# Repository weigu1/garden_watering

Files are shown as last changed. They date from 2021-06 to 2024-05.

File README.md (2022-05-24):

# Watering the garden with valves per MQTT over WiFi using an ESP8266

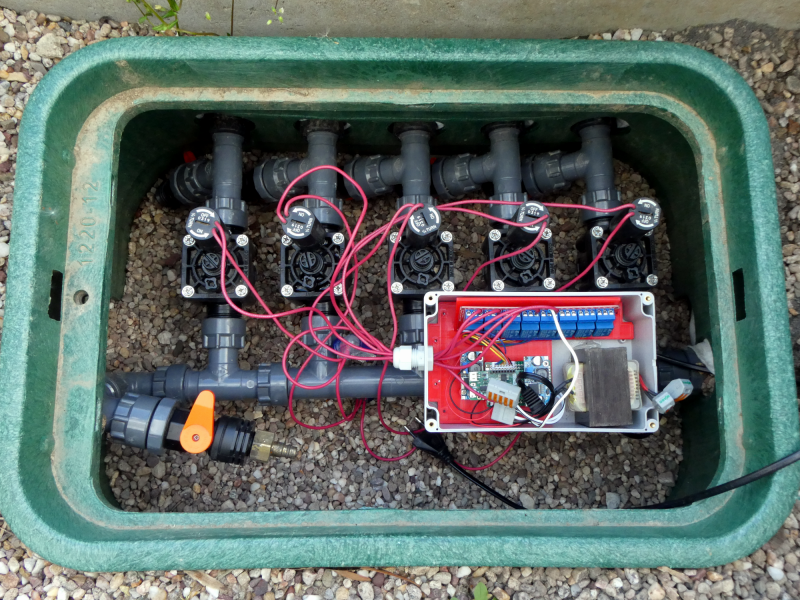
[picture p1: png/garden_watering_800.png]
garden_watering garden watering


## All infos on: <http://www.weigu.lu/microcontroller/garden_watering/index.html>

## Some infos

The vegetable garden must be regularly supplied with water. To save water, I use drip hoses, and to simplify my life, I have automated the control of the irrigation.

It began with a command of a box with 5 magnetic valves from Hunter. The box contained 5 valves Hunter PGV 101 MMB (3/4", 25&#8239;mm). The valves need 24&#8239;VAC, so we need a transformer. As the valves are never open at the same time a current of 1&#8239;A should suffice. There are cheap relay shields out there with Optocoupler, perfect for this project. An ESP8266 ([Lolin/Wemos D1 mini pro V2 ](https://www.wemos.cc/en/latest/d1/d1_mini_pro.html)) connects us with the network over WiFi and MQTT and is used to send commands and get data. The ESP8266 board is also powered by the transformer. This is done with a LM2596 DC/DC buck converter breakout board.

As the whole thing is contained in a  IP65 waterproof enclosure, I wanted to monitor temperature and humidity in the box and added a BMP280 sensor. A piece of PLA from my 3D printer created with FreeCAD (files on git) helped to connect everything together.

### BOM

- 5 valves Hunter PGV 101 MMB (3/4", 25&#8239;mm, 24&#8239;VAC)
- Trafo 24&#8239;VAC
- 8 Channel DC 5&#8239;V AC 230&#8239;V Relay Shield with Optocoupler
- LM2596 DC/DC Buck Converter
- Lolin/Wemos D1 mini pro V2
- BMP280 breakout board
- BOPLA ET-237 Euromas II, 200x120x90&#8239;mm³, IP65

### Software

The software communicates per `MQTT` over `WiFi`. It uses my ESPToolbox library for WiFi and logging functions and to get the time. To avoid version problems the lib is included in the sketch folder. Programming is done over OTA.

We get two topics:

```C
    String MQTT_TOPIC_OUT = "weigu/garden/watering/data";
    String MQTT_TOPIC_IN = "weigu/garden/watering/command";
```

Commands are in JSON and have the following JSON format (I eliminated the square brackets in the new version 1.1 because openHAB had problems with those when transforming):

```json
    {"Relay_(0-4)":4,"Time_min":20}
    {"Auto_(0-1)":1} 
    {"Event_(nr_relay_start_duration)":"3 3 2021 5"}   
```

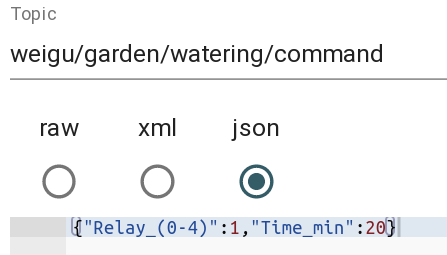
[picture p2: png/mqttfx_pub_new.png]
mqtt publish


+ With the first command you can start or stop manually the watering of a relay. Watering stops automatically after x minutes. To stop manually the time is set to zero: `{"Relay_(0-4)":4,"Time_min":0}`

+ The second command (version 1.1) switches automatic watering on (1) or off (0).

+ With the third command (version 1.1) we can also change via MQTT the watering events in the events array. Supported are up to 10 (0-9) events. Default are 5 events but you can add events in the `config.h` file. In the automated watering array we define the start times of a relay and duration of watering events. If we want e.g. that relay 3 opens at 15h15 for 15 minutes we add the line: `{3,1515,15}` to the array. With the command: `{"Event_(nr_relay_start_duration)":"3 3 2021 5"}` we can change this. The first number is the event number (0-9).   

The following is seen on the data channel:

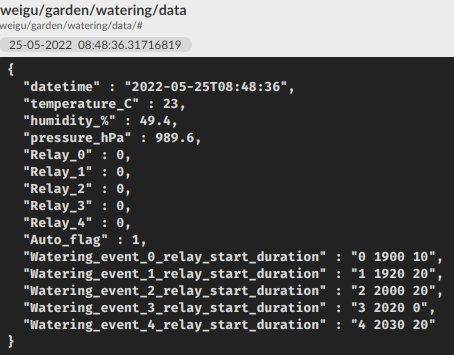
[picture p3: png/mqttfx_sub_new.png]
mqtt subscribe


In the new version  (1.1) all relevant data you must or can change are in a config (`config.h`) file, also contained in the main folder. You can also place this file in the sketchbook/library folder named `Secrets` and rename it to your needs (e.g. `secrets.h`).

In the main file (.ino) you can activate or deactivate features by commenting or uncommenting some lines. Here you must activate `USE_SECRETS`:

In the `config.h` file, you must change the WiFi parameter and the MQTT server address. In the automated watering array we define the start times and duration of watering events.

Other things we perhaps want to change are the publishing interval `PUBLISH_TIME` or the MQTT topics.

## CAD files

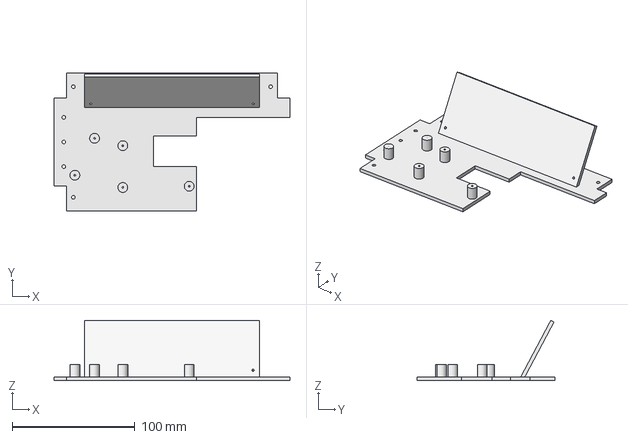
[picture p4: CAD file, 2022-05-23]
FreeCAD/pcb_holder.FCStd
192.0 x 112.0 x 49.1 mm

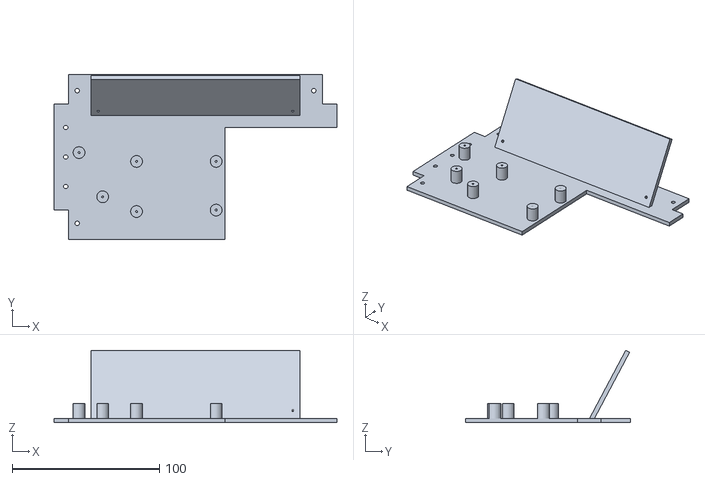
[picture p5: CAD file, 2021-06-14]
FreeCAD/pcb_holder-Fusion001.stl
192.0 x 112.0 x 49.1

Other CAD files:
FreeCAD/pcb_holder.stl

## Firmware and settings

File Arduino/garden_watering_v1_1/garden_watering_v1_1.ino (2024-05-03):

/*
  garden_watering.ino

  V1.1 2022-05-23
  changes from v1.0: added config file, mqtt secure bug, added scheduled
                     erigation.
                      
  for infos over time:
  https://www.weigu.lu/microcontroller/tips_tricks/esp_NTP_tips_tricks/index.html                   

  ---------------------------------------------------------------------------
  Copyright (C) 2022 Guy WEILER www.weigu.lu
  
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
  This program is distributed in the hope that it will be useful,
  but WITHOUT ANY WARRANTY; without even the implied warranty of
  MERCHANTABILITY or FITNESS FOR A PARTICULAR PURPOSE.  See the
  GNU General Public License for more details.
  You should have received a copy of the GNU General Public License
  along with this program.  If not, see <https://www.gnu.org/licenses/>.
  ---------------------------------------------------------------------------
 
  ESP8266: LOLIN/WEMOS D1 mini pro
  ESP32:   MH ET LIVE ESP32-MINI-KIT 
  
  MHET    | MHET    - LOLIN        |---| LOLIN      - MHET    | MHET
  
  GND     | RST     - RST          |---| TxD        - RxD(3)  | GND
   NC     | SVP(36) -  A0          |---| RxD        - TxD(1)  | 27 
  SVN(39) | 26      -  D0(16)      |---|  D1(5,SCL) -  22     | 25
   35     | 18      -  D5(14,SCK)  |---|  D2(4,SDA) -  21     | 32
   33     | 19      -  D6(12,MISO) |---|  D3(0)     -  17     | TDI(12)
   34     | 23      -  D7(13,MOSI) |---|  D4(2,LED) -  16     | 4
  TMS(14) | 5       -  D8(15,SS)   |---| GND        - GND     | 0   
   NC     | 3V3     - 3V3          |---|  5V        -  5V     | 2
  SD2(9)  | TCK(13)                |---|              TD0(15) | SD1(8)
  CMD(11) | SD3(10)                |---|              SD0(7)  | CLK(6)
*/

/*!!!!!!!!!! make your changes in config.h (or secrets.h) !!!!!!!!!*/

/*!!!!!!!!!! to debug you can use the onboard LED, a second serial port on D4
             or best: UDP! Look in setup()                !!!!!!!!!*/
             
/*?????? Comment or uncomment the following lines suiting your needs ??????*/

/* The file "secrets.h" (here secrets_garden.h) has to be placed in the sketchbook libraries folder
   in a folder named "Secrets" and must contain the same things than the file config.h*/
#define USE_SECRETS
#define OTA               // if Over The Air update needed (security risk!)
//#define MQTTPASSWORD    // if you want an MQTT connection with password (recommended!!)
#define STATIC            // if static IP needed (no DHCP)
#define BME280_I2C       

/****** Arduino libraries needed ******/
#ifdef USE_SECRETS
  #include <secrets_garden_watering.h>
#else  
  #include "config.h"      // most of the things you need to change are here
#endif // USE_SECRETS  
#include "ESPToolbox.h"  // ESP helper lib (more on weigu.lu)
#include <PubSubClient.h>
#include <ArduinoJson.h>
#ifdef BME280_I2C
  #include <Wire.h>
  #include <BME280I2C.h>
#endif

/****** WiFi and network settings ******/
const char *WIFI_SSID = MY_WIFI_SSID;           // if no secrets file, use the config.h file
const char *WIFI_PASSWORD = MY_WIFI_PASSWORD;   // if no secrets file, use the config.h file
#ifdef OTA                                // Over The Air update settings
  const char *OTA_NAME = MY_OTA_NAME;
  const char *OTA_PASS_HASH = MY_OTA_PASS_HASH;  // use the config.h file
#endif // ifdef OTA      
#ifdef STATIC
  IPAddress NET_LOCAL_IP (NET_LOCAL_IP_BYTES);    // 3x optional for static IP
  IPAddress NET_GATEWAY (NET_GATEWAY_BYTES);      // look in config.h
  IPAddress NET_MASK (NET_MASK_BYTES);  
#endif // ifdef STATIC
IPAddress UDP_LOG_PC_IP(UDP_LOG_PC_IP_BYTES);     // UDP logging if enabled in setup() (config.h)

/****** MQTT settings ******/
const int MQTT_MAXIMUM_PACKET_SIZE = 2048; // in setup()
const short MQTT_PORT = MY_MQTT_PORT;
WiFiClient espClient;
#ifdef MQTTPASSWORD
  const char *MQTT_USER = MY_MQTT_USER;
  const char *MQTT_PASS = MY_MQTT_PASS;
#endif // MQTTPASSWORD

PubSubClient MQTT_Client(espClient);

/******* BME280 ******/
float temp(NAN), hum(NAN), pres(NAN);
#ifdef BME280_I2C
  BME280I2C bme;    // Default : forced mode, standby time = 1000 ms
                    // Oversampling = pressure ×1, temperature ×1, humidity ×1, filter off,
#endif

ESPToolbox Tb;

/********** SETUP ************************************************************/
void setup() {
  Tb.set_led_log(true);                 // use builtin LED for debugging
  //Tb.set_serial_log(true,1);        // 2 parameter = interface (1 = Serial1)  
  Tb.set_udp_log(true, UDP_LOG_PC_IP, UDP_LOG_PORT); // use "nc -kulw 0 7777"    
  Tb.init_ntp_time();  
  init_wifi();       
  init_relays(PIN_RELAYS,sizeof(PIN_RELAYS));
  #ifdef BME280_I2C
    init_bme280();     
  #endif
  delay(2000);                                  // give it some time   
  MQTT_Client.setBufferSize(MQTT_MAXIMUM_PACKET_SIZE);
  MQTT_Client.setServer(MQTT_SERVER,MQTT_PORT); //open connection MQTT server
  MQTT_Client.setCallback(MQTT_callback);
  //mqtt_connect();
  #ifdef OTA
    Tb.init_ota(OTA_NAME, OTA_PASS_HASH);
  #endif // ifdef OTA
  Tb.blink_led_x_times(3);
  Tb.log_ln("Setup done!");
}

/********** LOOP  ************************************************************/

void loop() {
  #ifdef OTA
    ArduinoOTA.handle();
  #endif // ifdef OTA
  Tb.get_time();
  handle_relays();
  handle_auto_watering();
  // Publish every PUBLISH_TIME  
  if (Tb.non_blocking_delay(PUBLISH_TIME)) {    
    MQTT_get_temp_and_publish();        
  }    
  if (WiFi.status() != WL_CONNECTED) {   // if WiFi disconnected, reconnect
    init_wifi();
  }    
  if (!MQTT_Client.connected()) {        // reconnect mqtt client, if needed  
    mqtt_connect();
  }
  MQTT_Client.loop();                    // make the MQTT live  
  delay(10); // needed for the watchdog!
}

/********** WiFi functions ***************************************************/

// init WiFi (overloaded function if STATIC)
void init_wifi() {
  #ifdef STATIC
    Tb.init_wifi_sta(WIFI_SSID, WIFI_PASSWORD, NET_HOSTNAME, NET_LOCAL_IP,
                  NET_GATEWAY, NET_MASK);
  #else                  
    Tb.init_wifi_sta(WIFI_SSID, WIFI_PASSWORD, NET_MDNSNAME, NET_HOSTNAME);                       
  #endif // ifdef STATIC
}

/********** MQTT functions ***************************************************/

// connect to MQTT server
void mqtt_connect() {
  while (!MQTT_Client.connected()) { // Loop until we're reconnected
    Tb.log("Attempting MQTT connection...");    
    #ifdef MQTTPASSWORD
      if (MQTT_Client.connect(MQTT_CLIENT_ID, MQTT_USER, MQTT_PASS)) {
    #else
      if (MQTT_Client.connect(MQTT_CLIENT_ID)) { // Attempt to connect
    #endif // ifdef UNMQTTSECURE
      Tb.log_ln("MQTT connected");      
      MQTT_Client.subscribe(MQTT_TOPIC_IN.c_str());
      // Once connected, publish an announcement...    
      // MQTT_Client.publish(MQTT_TOPIC, "{\"dt\":\"connected\"}");
      // don't because OpenHAB does not like this ...      
    }
    else {
      Tb.log("MQTT connection failed, rc=");
      Tb.log(String(MQTT_Client.state()));
      Tb.log_ln(" try again in 5 seconds");
      delay(5000);  // Wait 5 seconds before retrying
    }
  }
}

// MQTT get the time, relay flags ant temperature an publish the data
void MQTT_get_temp_and_publish() {
  DynamicJsonDocument doc_out(1024);
  String mqtt_msg, we_msg;  
  doc_out["datetime"] = Tb.t.datetime;
  #ifdef BME280_I2C
    get_data_bme280();
    doc_out["temperature_C"] = (int)(temp*10.0 + 0.5)/10.0;
    doc_out["humidity_%"] = (int)(hum*10.0 + 0.5)/10.0;
    doc_out["pressure_hPa"] = (int)((pres + 5)/10)/10.0;
  #endif    
  doc_out["Relay_0"] = (byte)!relay_stop_flags[0];
  doc_out["Relay_1"] = (byte)!relay_stop_flags[1];
  doc_out["Relay_2"] = (byte)!relay_stop_flags[2];
  doc_out["Relay_3"] = (byte)!relay_stop_flags[3];
  doc_out["Relay_4"] = (byte)!relay_stop_flags[4];
  doc_out["Auto_flag"] = (byte)auto_flag;    
  for (byte i=0; i<(sizeof(watering_events)/sizeof(watering_events[0])); i++) {
    we_msg = String(watering_events[i].relay_nr) + ' ' +
             String(watering_events[i].start_time) + ' ' +
             String(watering_events[i].duration);
    doc_out["Watering_event_" + String(i) + "_relay_start_duration"] = we_msg;
  }
  mqtt_msg = "";
  serializeJson(doc_out, mqtt_msg);
  MQTT_Client.publish(MQTT_TOPIC_OUT.c_str(),mqtt_msg.c_str());    
  Tb.log("MQTT published at ");
  Tb.log_ln(Tb.t.time);
}  

// MQTT callback
// Commands in JSON: {"Relay_(0-4)":1,"Time_min":20}
//                   {"Auto_(0-1)":1}
//                   {"Event_(nr_relay_start_duration)":"2 3 1900 15"}

void MQTT_callback(char* topic, byte* payload, unsigned int length) {
  DynamicJsonDocument doc_in(256);
  byte nr;
  unsigned int i, tmp;
  unsigned long time_ms;
  String message;
  Tb.log_ln("Message arrived [" + String(topic) + "] ");
  for (int i=0;i<length;i++) {    
    message += String((char)payload[i]);
  }
  Tb.log_ln(message);
  deserializeJson(doc_in, message);
  if (doc_in.containsKey("Auto_(0-1)")) {
    auto_flag = bool(doc_in["Auto_(0-1)"]); 
    Tb.log_ln("Auto_flag arrived [" + String(auto_flag) + "] ");
  }
  else if (doc_in.containsKey("Event_(nr_relay_start_duration)")) {
      String event_str = doc_in["Event_(nr_relay_start_duration)"]; 
      Tb.log_ln(event_str);
      i = event_str.substring(0,1).toInt();      
      tmp = event_str.substring(2,3).toInt();
      watering_events[i].relay_nr = tmp;
      tmp = event_str.substring(4,8).toInt();
      watering_events[i].start_time = tmp;
      tmp = event_str.substring(9).toInt();
      watering_events[i].duration = tmp;  
  }
  else {
    nr = doc_in["Relay_(0-4)"];  
    time_ms = doc_in["Time_min"];
    time_ms = time_ms * 60UL *1000UL;  
    Tb.log_ln("Nr: " + String(nr) + " time: " + String(time_ms));
    if ((nr >= 0) && (nr < NR_OF_RELAYS)) {    
      if (time_ms != 0) {
        relay_times_ms[nr] = time_ms;
        relay_start_flags[nr] = true;
      }
      else {
        relay_times_ms[nr] = 0;
      }    
    }
  }  
}

/********** BME280 functions *************************************************/

// initialise the BME280 sensor
#ifdef BME280_I2C
  void init_bme280() {
    Wire.begin();
    while(!bme.begin()) {
      Tb.log_ln("Could not find BME280 sensor!");
      delay(1000);
    }
    switch(bme.chipModel())  {
       case BME280::ChipModel_BME280:
         Tb.log_ln("Found BME280 sensor! Success.");
         break;
       case BME280::ChipModel_BMP280:
         Tb.log_ln("Found BMP280 sensor! No Humidity available.");
         break;
       default:
         Tb.log_ln("Found UNKNOWN sensor! Error!");
    }
  }

// get BME280 data and log it
void get_data_bme280() {
  BME280::TempUnit tempUnit(BME280::TempUnit_Celsius);
  BME280::PresUnit presUnit(BME280::PresUnit_Pa);
  bme.read(pres, temp, hum, tempUnit, presUnit);
  Tb.log_ln("Temp: " + (String(temp)) + " Hum: " + (String(hum)) + 
           " Pres: " + (String(pres)));
}
#endif  // BME280_I2C

/********** Relay functions **************************************************/

// init relay pins as output and close all relays
void init_relays(const byte PIN_RELAYS[], byte number_of_relays) {
  for (byte i=0; i<number_of_relays; i++) {
    pinMode(PIN_RELAYS[i],OUTPUT);
  }
  for (byte i=0; i<number_of_relays; i++) {  // all off (neg. logic!)
    digitalWrite(PIN_RELAYS[i],HIGH);
  }
}

// handle auto watering (array in config.h)
void handle_auto_watering() {
  byte nr;
  unsigned long time_ms;
  static unsigned int one_minute_flag = 0;
  if (auto_flag) {
    if (one_minute_flag == (Tb.t.hour*100+Tb.t.minute)) { // wait one minute    
      Tb.log(".");      
    }
    else {          
      for (byte i=0; i<(sizeof(watering_events)/sizeof(watering_events[0])); i++) {        
        if ((Tb.t.hour*100+Tb.t.minute)==watering_events[i].start_time) {          
          one_minute_flag = watering_events[i].start_time;
          Tb.log_ln("auto_watering_started at " + String(Tb.t.time));
          nr = watering_events[i].relay_nr;
          time_ms = watering_events[i].duration;
          time_ms = time_ms * 60UL *1000UL;  
          if ((nr >= 0) && (nr < NR_OF_RELAYS)) {    
            if (time_ms != 0) {
              relay_times_ms[nr] = time_ms;
              relay_start_flags[nr] = true;
            }
            else {
              relay_times_ms[nr] = 0;
            }              
          }
        }
      }      
    }
  }  
}

// start watering if start flag = true and stop it if time is over

void handle_relays() {
  for (byte i=0; i<5; i++) {
    if (relay_start_flags[i] == true) {
      relay_start_flags[i] = false;
      relay_stop_flags[i] = false;
      digitalWrite(PIN_RELAYS[i],LOW);
      relay_prev_millis[i] = millis(); 
      Tb.log_ln("Relay Nr: " + String(i) + " started (" + String(millis()) + ')');
    }  
    if (relay_stop_flags[i] == false) {      
      if ((millis() - relay_prev_millis[i]) > relay_times_ms[i]) {
        relay_stop_flags[i] = true;
        digitalWrite(PIN_RELAYS[i],HIGH);      
        Tb.log_ln("Relay Nr: " + String(i) + " stopped (" + String(millis()) + ')');
      }
    }
  }
}

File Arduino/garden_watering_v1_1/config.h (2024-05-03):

/*!!!!!! Things you must change: !!!!!!*/

/****** WiFi SSID and PASSWORD ******/
const char *MY_WIFI_SSID = "your_ssid";
const char *MY_WIFI_PASSWORD = "your_password";

/****** MQTT settings ******/
const char *MQTT_SERVER = "192.168.178.222";

/*+++++++ Things you can change: +++++++*/

/******* Automated watering array *******/
bool auto_flag = 1;
struct we {
  unsigned int relay_nr;
  unsigned int start_time;
  unsigned int duration;
};

// A triple of data per watering event:
// relay number, time (hr*100+min), minutes to water
// never use 2 relays at the same time

we watering_events[] = {
  {0,1900,5}, // relay number, time (hr*100+min), minutes to water
  {1,1910,10},
  {2,2000,0},
  {3,2030,0},
  {4,2055,0},
};  

/****** Publishes every in milliseconds ******/
const long PUBLISH_TIME = 10000;

/******* Relays *******/
const byte NR_OF_RELAYS = 5;
const byte PIN_RELAYS[NR_OF_RELAYS] = {16, 14, 12, 13, 0};
bool relay_start_flags[NR_OF_RELAYS] = {false,false,false,false,false};
bool relay_stop_flags[NR_OF_RELAYS] = {true,true,true,true,true};
unsigned long relay_times_ms[NR_OF_RELAYS] = {10000,20000,30000,40000,50000};
unsigned long relay_prev_millis[NR_OF_RELAYS] = {0,0,0,0,0};

/****** MQTT settings ******/
const int MQTT_MAXIMUM_PACKET_SIZE = 1024; // look in setup()
const char *MQTT_CLIENT_ID = "garden_watering"; // this must be unique!!!
String MQTT_TOPIC_OUT = "weigu/garden/watering/data";
String MQTT_TOPIC_IN = "weigu/garden/watering/command";
const short MY_MQTT_PORT = 1883; // or 8883
// only if you use MQTTPASSWORD (uncomment //#define MQTTPASSWORD in ino file)
const char *MY_MQTT_USER = "me";
const char *MY_MQTT_PASS = "meagain";

/****** WiFi and network settings ******/
const char *NET_MDNSNAME = "watering";      // optional (access with SmartyReaderLAM.local)
const char *NET_HOSTNAME = "watering";      // optional
const word UDP_LOG_PORT = 6666;             // UDP logging settings if enabled in setup()
const byte UDP_LOG_PC_IP_BYTES[4] = {192, 168, 1, 50};
const char *NTP_SERVER = "lu.pool.ntp.org"; // NTP settings
// your time zone (https://remotemonitoringsystems.ca/time-zone-abbreviations.php)
const char *TZ_INFO    = "CET-1CEST-2,M3.5.0/02:00:00,M10.5.0/03:00:00";

// only if you use OTA (uncomment //#define OTA in ino file)
const char *MY_OTA_NAME = "garden_watering"; // optional (access with garden_watering.local)
// Linux Create Hasgh with: echo -n 'P@ssword1' | md5sum
const char *MY_OTA_PASS_HASH = "myHash";     // Hash for password

// only if you use a static address (uncomment //#define STATIC in ino file)
const byte NET_LOCAL_IP_BYTES[4] = {192, 168, 178, 155};
const byte NET_GATEWAY_BYTES[4] = {192, 168, 178, 1};
const byte NET_MASK_BYTES[4] = {255,255,255,0};  

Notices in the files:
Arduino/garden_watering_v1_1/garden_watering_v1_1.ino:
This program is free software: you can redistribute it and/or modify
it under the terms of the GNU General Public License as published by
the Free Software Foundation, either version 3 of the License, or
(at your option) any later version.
